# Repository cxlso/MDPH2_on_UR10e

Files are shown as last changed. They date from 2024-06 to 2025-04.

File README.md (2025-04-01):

# MDPH2 on UR10e
###### A controller box and mounts to get started with the Massive Dimension thermoplastic extruder MDPH2 on UR10e

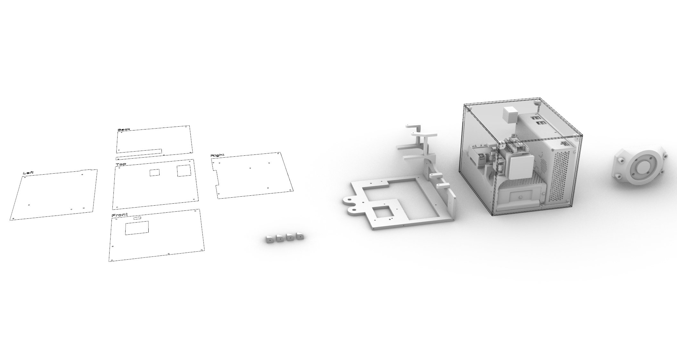
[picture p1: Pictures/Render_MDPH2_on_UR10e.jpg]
Render_MDPH2_on_UR10e


## Overview
This repository contains everything needed to get started with robotic thermoplastic printing with the [MDPH2 from Massive Dimension](https://massivedimension.com/products/mdphe-v1-pellet-head-extruder-system) and the [Universal Robot UR10e](https://www.universal-robots.com/products/ur10-robot/) (or any UR model capable of handeling the weight).

Included in the repository are:

- Controller Box CAD Files: For 3D printing the structure and laser cutting the acrylic walls of the controller box,
- Controller Box Wiring Diagram: For wiring the electronic componenent of the controller box,
- Mounts CAD File: For 3d printing mounts to secure the extruder,
- Scripts: Arduino code for the controller and Grasshopper toolpath example.

## Note on the Signal Workflow

The workflow begins with the Grasshopper script embedding the extrusion commands (rate and direction) into the URP file. This file instructs the UR10e to output two analog voltage signals (0-5V) on AO0 (Pul) and AO1 (Dir). These signals are read by the Arduino on pins A0 (Pul) and A1 (Dir), which translates them into digital signals on pins D2 (Pul) and D3 (Dir) for the ClearPath servo motor of the MDPH2.

The analog signals can also be overwritten in real-time using the UR Teaching Pendant. 

**Grasshopper (Extrusion Command Embeded in URP file/G-Code ) ⟶ UR10e (Analog Output 0-5V) ⟶ Arduino (Analog Input) ⟶ MDPH2's Servo Motor (Digital Signal)**

**Note:** The temperature is not controlled by the Grasshopper script. The temperature must be set manually on the PID controller. Allow the extruder to warm up to the desired temperature before starting extrusion to prevent motor damage due to high torque.  
For PLA, we set the temperature to 190°C. It is recommended to stay on the lower end of the melting temperature spectrum to maintain high viscosity, reduce stringing, and minimize cooling time.

## Components

- Arduino Nano
- LM2596 Stepdown reducer 24v to 12v
- Rocker Switch
- Inkbird ITC-100 PID Temperature Controller (comes with the MDPH2)
- IPC-5 75v Power Supply (comes with the MDPH2)
- Solid State Relay (comes with the MDPH2)
- 24v Power Supply
- M3 and M4 Hex Socket Head Screws
- 3mm Acrylic Sheet
- Electrical Connectors (JST XH in our case)
- 18 and 24awg cables 

## Setup and Installation

### Prerequisites

- UR10e Robotic Arm (or any UR models),
- Massive Dimension MDPH2 Thermoplastic extruder,
- Rhino Grasshopper: For generating toolpath commands.

### Wiring Diagram

Refer to the following wiring diagram for the electrical connections.

MDPH2_on_UR10e_Wire_Diagram
Diagram made with the open-source tool [Fritzing](https://fritzing.org/).

### Controller Box and Mount CAD Files

- [MDPH2 Extruder Mount](Mount/Print_MD_Extruder_Mount.stl) 3D printing file,
- [Structure](Controller_Box/CAD/Print_MD_Skeleton.stl) 3D printing file. Skeleton inside de box holding all the components in place,
- [Corner brackets](Controller_Box/CAD/Print_MD_Corner_Bracket.stl) 3D printing file,
- [3MM acrylic wall](Controller_Box/CAD/Cut_MD_3MM_Walls.AI) Laser cutting file.

### Scripts

#### [Arduino Script](Arduino/Stepper_PulseDir_MD)

Upload the provided code to the Arduino Nano. Ensure all connections are made according to the wiring diagram.

#### [Grasshopper Definition](Grasshopper/Basic_Robotic_Extrusion_MDPH2.gh)

The [Robots](https://www.food4rhino.com/en/app/robots) plugin is necessary. The extrusion rate is set in RPM and is converted to steps per second with the following equation:
$$y = \left( \frac{x \times 800}{60} \right)$$
Where 800 represents the number of steps per revolution for the stepper motor, and 60 is used to convert minutes to seconds, resulting in the conversion of RPM (x) to steps per second (y).

The actual RPM can be checked through [ClearPath MSP](https://www.teknic.com/files/downloads/motor_setup.zip) via the micro USB cable on top of the servo motor.

The mass and center of gravity can be found in the Grasshopper script. These settings are very important for this extruder as it is reaching the load capacity of the UR10e. 

## Photos and Videos

https://github.com/cxlso/MDPH2_on_UR10e/assets/29285706/ac5a9cc8-03f6-4395-85b4-7b0d291706e9

https://github.com/cxlso/MDPH2_on_UR10e/assets/29285706/749127e9-4e9b-446a-b5af-80f2f0c1dffd

     

## Contributing

Contributions are welcome! Please submit a pull request or open an issue to discuss any changes or improvements.

## License

[][cc-by-nc-sa]

This work is licensed under a
[Creative Commons Attribution-NonCommercial-ShareAlike 4.0 International License][cc-by-nc-sa].

[][cc-by-nc-sa]

[cc-by-nc-sa]: http://creativecommons.org/licenses/by-nc-sa/4.0/
[cc-by-nc-sa-image]: https://licensebuttons.net/l/by-nc-sa/4.0/88x31.png
[cc-by-nc-sa-shield]: https://img.shields.io/badge/License-CC%20BY--NC--SA%204.0-lightgrey.svg

## Acknowledgements

Special thanks to [Luigi Pacheco](https://luigipacheco.com/) and [Bhavleen Kaur](https://bhavleenkaurnarula.wordpress.com/) from the [FIU RDFlab](https://rdflabfiu.github.io/labwiki/) for the tips.

This project was developed on my own initiative at the [School of Architecture of Florida Atlantic University](https://www.fau.edu/artsandletters/architecture/) within the Environmental Design and Natural Materials lab, directed by Shermeen Yousif.

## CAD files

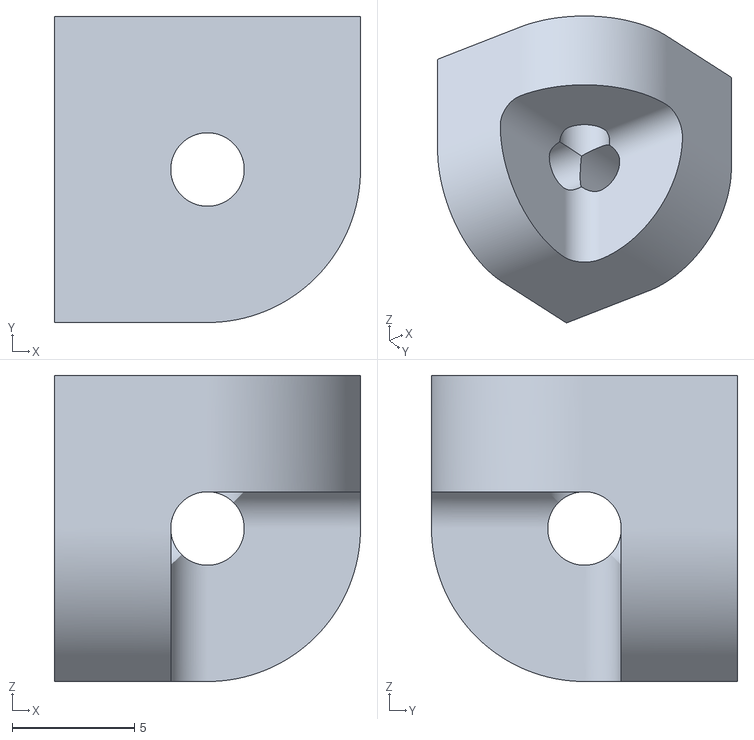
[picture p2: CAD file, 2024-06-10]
Controller_Box/CAD/Print_MD_Corner_Bracket.stl
12.5 x 12.5 x 12.5

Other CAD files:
Controller_Box/CAD/Parts/Relay_SSR-40_DA.3dm
Mount/UR10e_Flange.3dm

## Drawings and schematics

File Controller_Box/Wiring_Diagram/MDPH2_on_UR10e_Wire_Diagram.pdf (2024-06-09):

# 110/220V AC

# Extruder Controller Box

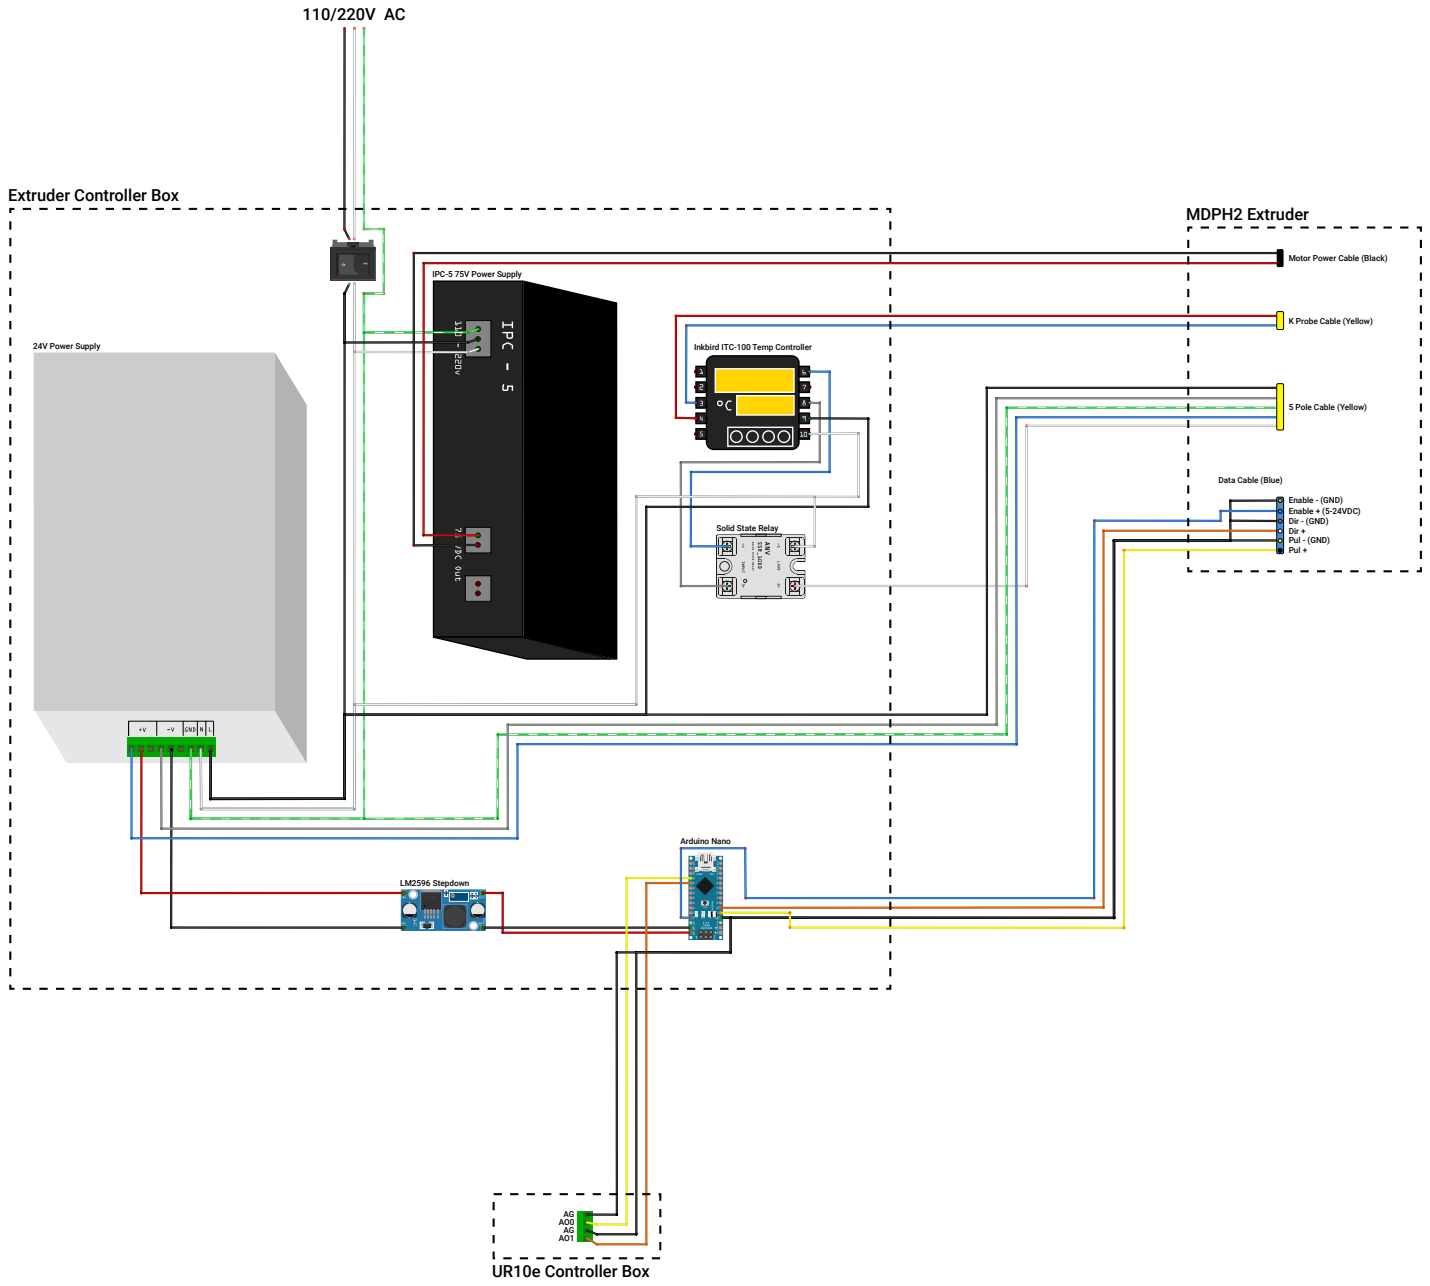
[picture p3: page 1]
24V Power Supply; Arduino Nano; UR10e Controller Box; MDPH2 Extruder; LM2596 Stepdown; Enable - (GND) Enable + (5-24VDC) Dir - (GND) Dir + Pul - (GND) Pul +

Motor Power Cable (Black)

IPC-5 75V Power Supply

K Probe Cable (Yellow)

Inkbird ITC-100 Temp Controller

5 Pole Cable (Yellow)

Data Cable (Blue)

Solid State Relay

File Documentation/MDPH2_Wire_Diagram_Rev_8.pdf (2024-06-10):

## MDPH2 Wire Diagram

Located On MDPH2 Pellet Head White | Brown | Black

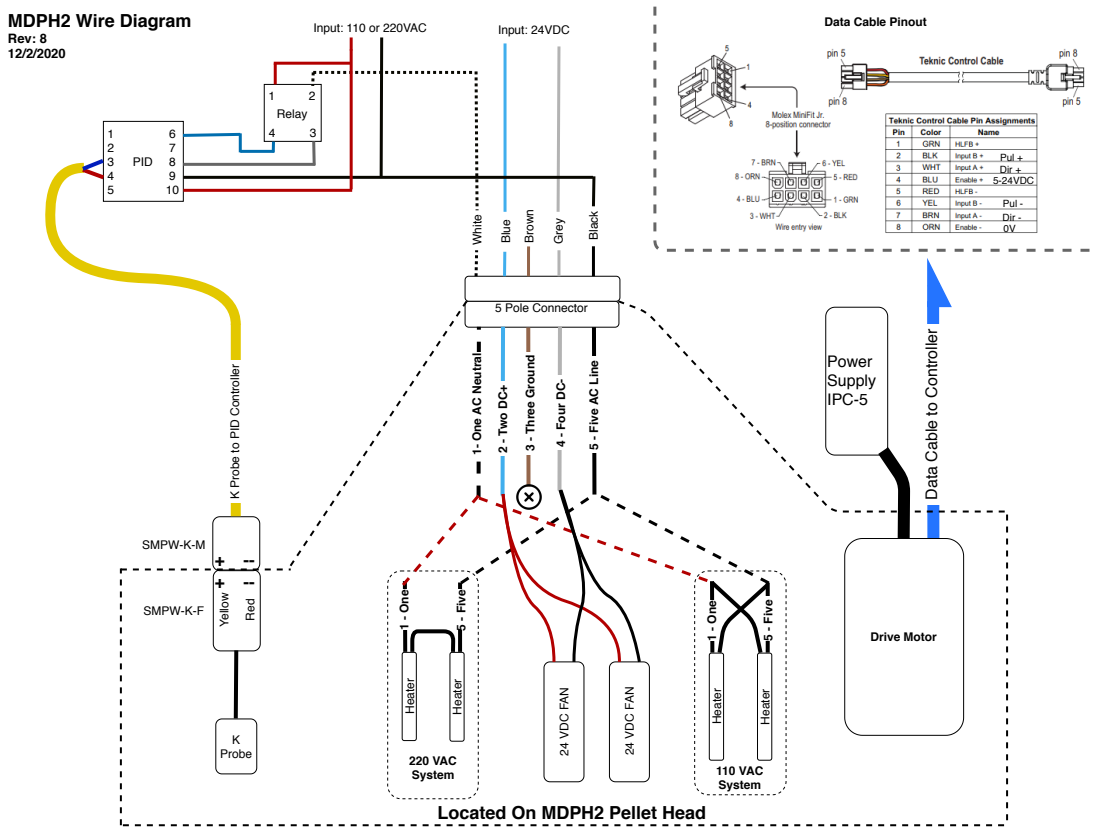
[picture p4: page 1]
5 Pole Connector; 2 - Two DC+; 4 - Four DC-; 3 - Three Ground; 220 VAC; System Heater; Heater 1 ⁻ One; 5 ⁻ Five; 110 VAC; System Heater Heater; 1 - One; 5 - Five; SMPW-K-F; Rev: 8 12/2/2020; K Probe; + --Red Yellow; SMPW-K-M; 24 VDC FAN; PID; Relay; Input: 110 or 220VAC; Blue; Input: 24VDCGrey; 5-24VDC; Dir +; Pul +

Data Cable Pinout

Pul -
Dir -
Drive Motor Data Cable to Controller
Power
Supply
IPC-5

1- One AC Neutral

5 - Five AC Line

K Probe to PID Controller

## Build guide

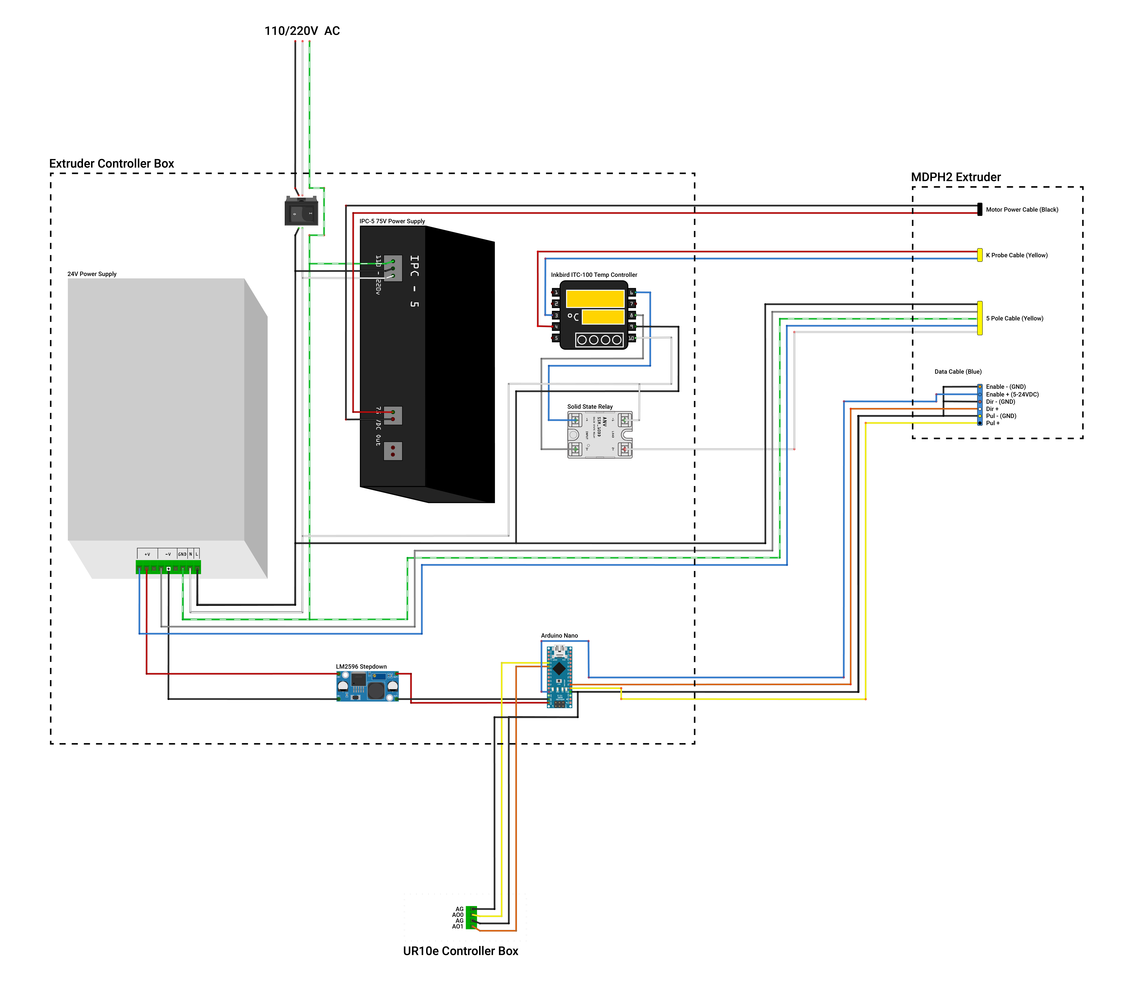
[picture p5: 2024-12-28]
Controller_Box/Wiring_Diagram/MDPH2_on_UR10e_Wire_Diagram.jpg

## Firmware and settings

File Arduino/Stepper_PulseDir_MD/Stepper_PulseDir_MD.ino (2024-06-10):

/*
  Stepper Motor Extruder Pulse and Direction

  This Arduino sketch controls a stepper motor using analog signals for speed (Pul/Step) and direction (Dir).

  Author:   cxlso (cxl.so)
  Year:     2024
  Version:  1

  Hardware Compatibility:
  - Stepper motor-based extruders (e.g., LDM WASP Extruders, Massive Dimension MDPH2 Extruder)

  Library Dependencies:
  - AccelStepper library (https://www.airspayce.com/mikem/arduino/AccelStepper/)

  License: GNU General Public License, version 2 or later (GPL-2.0-or-later) (https://www.gnu.org/licenses/gpl-2.0.html)
*/



#include <AccelStepper.h>

// Define driver digital pin connections
#define PulPin 2
#define DirPin 3
#define EnaPin 4

// Create a new AccelStepper object
AccelStepper stepper(AccelStepper::DRIVER, PulPin, DirPin);



void setup() {

  // Define stepper maximum speed in steps per second (steps/s)
  stepper.setMaxSpeed(4000);

  // Enable stepper
  pinMode(EnaPin, OUTPUT);
  digitalWrite(EnaPin, HIGH);

}



void loop() {

  // Read sensor values
  int Step_Reading = analogRead(A0);
  int Dir_Reading = analogRead(A1);

  // Limit minimum speed
  if (Step_Reading < 100) Step_Reading = 0;

  // Map Step_Reading to a speed range from 0 to 4000 steps/s
  int stepperMotorSpeed = map(Step_Reading, 0, 1023, 0, 4000);
  // Map Dir_Reading to a voltage range from 0V to 5V
  float stepperMotorDir = map(Dir_Reading, 0, 1023, 0, 5);

  // Set motor direction and speed
  if (stepperMotorDir > 0.5) {
    stepper.setSpeed(-stepperMotorSpeed);
  } else {
    stepper.setSpeed(stepperMotorSpeed);
  }
  stepper.runSpeed();
  
}

//Note: Arduino analog pins take from 0 to 5V and translate it to a digital range of 0 to 1023 (10 bits).
